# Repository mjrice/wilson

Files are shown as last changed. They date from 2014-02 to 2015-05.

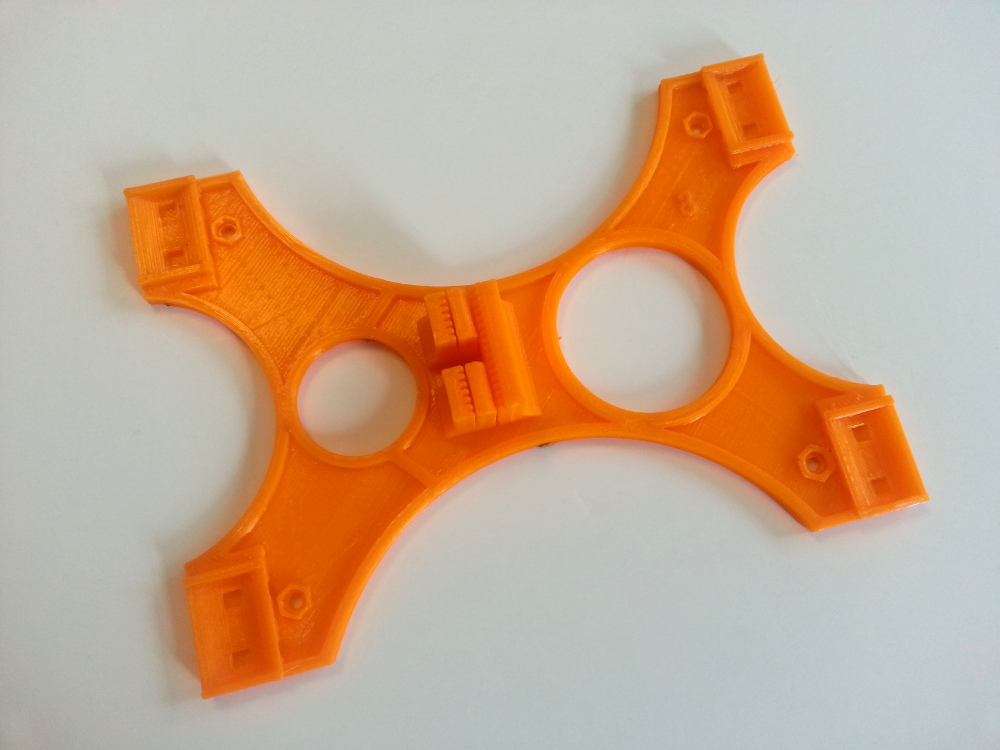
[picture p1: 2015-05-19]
doc/parts-visual/y-table.jpg

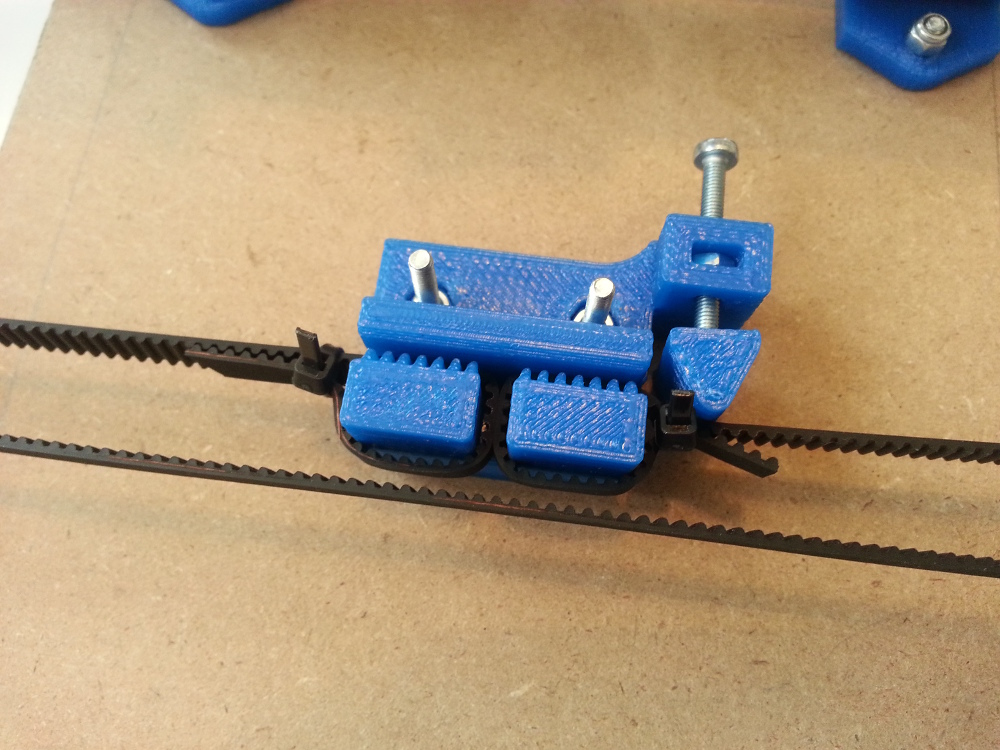
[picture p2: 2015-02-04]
doc/images/ts-belt-holder-assembled.jpg

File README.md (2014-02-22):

wilson
======

Reprap Wilson, 3D printer design
Published under GPL v3

This is my reprap printer design, a derivative from Josef Prusa's i3 with the
following goals:

1.  Replace the waterjet metal frame / wooden box frame with an inexpensive
	and rigid frame made from standard 2020 Aluminum Extrusion.

2.  To make the build volume parametric (easy to scale up or down by 50%), with
	a parametric BOM tool (spreedsheet) to assist in part selection.

3.  To simplify construction of the printer by reducing vitamins and including 
    detailed assembly steps as part of the design files.  I've made an effort 
	to reduce the number of unique parts (nuts & bolts) as much as possible.
	I've also incorporated single-piece Y ends that eliminate about 20 more
	hardware items.

The repository has these parts:

1. The STL files needed to build the printer.
2. Documentation section where instructions and parts-list can be found.
3. Some parts have corresponding OpenSCAD models which are kept in the scad 
   folder.
4. Various images of the printer/build process are in the images folder 
   (beneath docs).

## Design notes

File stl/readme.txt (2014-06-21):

There are two variants of the Repap Wilson design.  Some of the RP parts are common, and those STL files are located in this main directory.

The parts that are specific to one version or the other are located in the respective subfolders.

The BOM will tell you how many of which parts you will need to build the printer.

Notes about updates:

6/21/14 - I've modified a few models described below:

1. The Y belt holder now has a tensioner (yay) affixed to the side. Use
   a M3 x 20 or longer screw and nut to push the little round piece against
   the side of the belt after assembly.  

2. The fan duct for the extruder has been redesigned so that there are 
   separate outlets for the top of the hot end and below the nozzle.  This
   has been working great for me for PLA; ABS prints may not want that lower
   outlet blowing on the print so I'll archive the original fan duct as well.

3. The extruder body itself should now print better.  The opening for the 
   608 bearings on the sides has been marginally increased, as has been the
   J-Head hole on the bottom.  The opening for the hobbed bolt was cleared
   out to remove some extraneous support material.  Also, the distance 
   between the M3 screws for the hot end attachment was decreased by about
   1mm to get a better grip on the J-Head.

4. The Y ends for the TS were changed just a wee bit to make the holes come
   out more suitable (when sliced and printed with a .5mm nozzle) and also
   to add .5mm of height to the feet so that the printer won't tend to rock
   on the central frame.

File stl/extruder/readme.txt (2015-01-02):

Reprap Wilson Extruder files 
----------------------------

The extruder files located here are for the direct-drive extruder that I designed for Wilson.  

The parts for the original geared extruder have been moved to stl/alts.

NOTE!  The default direct-drive extruder is expecting you to use 1.75mm filament.  If you are going to use 3mm filament, I recommend building the geared extruder instead.

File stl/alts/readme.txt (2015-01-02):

wilson/stl/alts - home of old or alternate version of models.  You probably don't need these, unless you do.

belt-guide-sleeve-624.stl                    - An alternate version of the bearing holder.
biggear.stl                                  - Big gear for the Greg's style geared extruder
duct-xlong.stl                               - Another duct option for the extruder
extruder-body-clampmountstyle-1.75mm.stl     - An alternate body for the geared extruder that uses the clamp mount
extruder-body-clampmountstyle.stl            - An alternate body for the geared extruder that uses the clamp mount (3mm filament)
extruder-body.stl                            - The original geared extruder (this is what I used in the original videos)
FAN-DUCT-E3D.stl                             - An attempt to make a fan duct suited to the e3d v6.
FAN-DUCT-widemouth.stl                       - Yet another fan duct
fullgraphicsmartcontroller-mount.stl         - Mounts for the full graphics smart controller 
gregs-wade-v5-mrice-idler-for-M4screws.stl   - The original idler for the geared extruder
idler.stl                                    - The idler for the geared extruder (M3 screws)
smallgear.stl                                - Small gear for the Greg's style geared extruder
nameplate.stl                                - decorative
x-carriage.stl                               - The original X carriage that prints flat (& uses zip ties)
y-bearing-holder-lm10uu.stl                  - An alternate bearing holder if you go with 10mm smooth rods for the y axis
y-bearing-holder.stl                         - The original LM8UU bearing holder that prints flat (& uses zip ties)
y-belt-holder-ts-htd3.stl                    - If you use HTD3 instead of GT2, you need this for the Y belt holder
y-idler-ts-10mm-rods.stl                     - Y idler end for 10mm smooth rods instead of 8mm.
y-motor-ts-10mm-rods.stl                     - Y motor end for 10mm smooth rods instead of 8mm.

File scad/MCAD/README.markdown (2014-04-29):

OpenSCAD MCAD Library (http://stillmaintained.com/elmom/MCAD)
=====================

This library contains components commonly used in designing and moching up
mechanical designs. It is currently unfinished and you can expect some API
changes, however many things are already working.

This library is licensed under the LGPL 2.1
See http://creativecommons.org/licenses/LGPL/2.1/ or the included file, lgpl-2.1.txt.

## Usage ##

You can import these files in your scripts with `use <MCAD/filename.scad>`, 
where 'filename' is one of the files listed below like 'motors' or 
'servos'. Some files include useful constants which will be available 
with `include <MCAD/filename.scad>`, which should be safe to use on all 
included files (ie. no top level code should create geometry). (There is 
a bug/feature that prevents including constants from files that 
"include" other files - see the openscad mailing list archives for more 
details. Since the maintainers aren't very responsive, may have to work 
around this somehow)

If you host your project in git, you can do `git submodule add URL PATH` in your
repo to import this library as a git submodule for easy usage. Then you need to do
a `git submodule update --init` after cloning. When you want to update the submodule,
do `cd PATH; git checkout master; git pull`. See `git help submodule` for more info.

Currently Provided Tools:

* involute_gears.scad (http://www.thingiverse.com/thing:3575):
    - gear()
    - bevel_gear()
    - bevel_gear_pair()

* gears.scad (Old version):
    - gear(number_of_teeth, circular_pitch OR diametrial_pitch, pressure_angle OPTIONAL, clearance OPTIONAL)

* motors.scad:
    - stepper_motor_mount(nema_standard, slide_distance OPTIONAL, mochup OPTIONAL)

Other tools (alpha and beta quality):

* nuts_and_bolts.scad: for creating metric and imperial bolt/nut holes
* bearing.scad: standard/custom bearings
* screw.scad: screws and augers
* materials.scad: color definitions for different materials
* stepper.scad: NEMA standard stepper outlines
* servos.scad: servo outlines
* boxes.scad: box with rounded corners
* triangles.scad: simple triangles

Very generally useful functions and constants:

* math.scad: general math functions
* constants.scad: mathematical constants
* curves.scad: mathematical functions defining curves
* units.scad: easy metric units
* utilities.scad: geometric funtions and misc. useful stuff
* teardrop.scad (http://www.thingiverse.com/thing:3457): parametric teardrop module
* shapes.scad: simple shapes by Catarina Mota

External utils that generate and and process openscad code:

* openscad_testing.py: testing code, see below
* openscad_utils.py: code for scraping function names etc.

## Development ##

You are welcome to fork this project in github and request pulls. I will try to
accomodate the community as much as possible in this. If for some reason you
want collaborator access, just ask.

Github is fun (and easy), but I can include code submissions and other
improvements directly, and have already included code from various sources
(thingiverse is great :)

### Code style ###
I'd prefer to have all included code nicely indented, at least at the block
level, and no extraneous whitespace. I'm used to indent with four spaces as
opposed to tabs or other mixes of whitespace, but at least try to choose a style
and stick to it.

### Testing ###
I've started a minimal testing infrastucture for OpenSCAD code. It's written in
python and uses py.test (might be compatible with Nose also). Just type `py.test`
inside the lib dir in a terminal and you should see a part of the tests passing
and tracebacks for failing tests. It's very simplistic still, but it should test
that no syntax errors occur at least.

The code is included in openscad_testing.py, and can be imported to be
used in other codebases.

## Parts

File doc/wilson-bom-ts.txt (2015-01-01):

Exported bom for Wilson TS from wilson-bom.ods 
Please see the ODS file for details.  
----------------------------------------------

Item                                    Quantity	Length / Notes

2020 Extrusions		
Vertical frame piece (sides)            2           400mm
Horizontal frame piece (top and bottom) 2           330mm
Y axis frame piece (TS only)            2           400mm

M8 Smooth Rods		
X-Axis                                  2           370mm
Y-Axis                                  2           400mm
Z-Axis                                  2           350mm

Threaded Rods		
M5 threaded rod for Z axis              2           325mm

Belts & Pulleys		
Y axis GT2 timing belt (w=6mm)          1           830mm
X axis GT2 timing belt (w=6mm)          1           900mm
GT2 pulley                              2           Want diameter 16-20mm

Nuts & Bolts		
M5 x 10mm machine screw                 51	
M5 hex nut                               2	
M5 t slot nut                           51	
M4 x 20mm machine screw                  7	
M4 hex nut                               7	
M3 x 10mm machine screw                 11	
M3 x 14mm machine screw                 24	
M3 x 30mm machine screw                 10
M3 x 50mm machine screw                  1	   this is for the hinged lever of the direct-dirve extruder
M3 hex nut                              18
M3 lock nut                             13	
M3 washer                               17         This number is approximate
M2 x 16mm machine screw	                 6	   These and M2 nuts for mounting end stops
M2 hex nut	                         6	

Printed Parts – Required		
X end idler                              1	
X end motor                              1	
X carriage                               1	
Y end idler                              1	
Y end motor                              1	
Y belt holder                            1	
Y axis bearing holder                    4         for lm8uu bearings
Z motor holder, left                     1	
Z motor holder, right                    1	
Z rod holder, left                       1	
Z rod holder, right                      1	
Z rear bracket                           2	
Z endstop holder                         1	
Frame brace                              4	
Idler bearing guide (pair)               2	
Extruder body / idler set                1	
Extruder big gear / small gear set       1	
Extruder fan duct                        1	
Belt guides	                         4         (two belt guides, one for each 624 bearing)

Printed Parts – Recommended		
Electronics frame mount (for RAMPS)	1	
Filament spool support (two pieces)	1	
SMART display frame mount (two pieces)	1	

Everything Else		
NEMA17 Stepper motor	                 5	
MDF board (6mm thick)	                 1	230mm by 230mm
Heat bed                                 1 	MK2a or whatever
Heat bed thermistor                      1
Glass bed	                         1	3mm borosilicate or picture frame glass 8.25" square
Controller (Mega/RAMPS, Rambo, etc)	 1	
Endstop (limit) switch	                 3	6mm x 10mm x 20mm
LM8UU Linear bearing	                12	can get away with 11 if you use only three on the X carriage
624 roller bearing                       2	
5mm to 5mm shaft couplers	         2	Can also use vinyl tubing instead
40mm x 40mm x 10mm fan	                 1	12V
80mm x 80mm fan	                         1	For use with RAMPS frame mount
Miniature zip ties	                20	This number is approximate
Extruder idler springs	                 2	High tension 
Bed leveling springs	                 4	Lower tension
Power Supply	                         1	Size appropriately for heat bed and extruder
Hot end	                                 1	Recommend Jhead
MK7 drive gear                           1	omit if you are building the geared extruder (see below)
Printer mount deck (optional)	         1	18” x 18” x 1/2” plywood works well.

The items below are for building with the geared extruder instead of the direct-drive extruder

M3 x 8mm machine screw                   1	for small gear
M3 x 60mm machine screw                  2         
M8 x 20mm smooth rod or grub screw       1	
M8 washers                               5         For alignment of hobbed bolt
M8 locknut                               1         For extruder bolt
Hobbed bolt	                         1	Recommend airwolf3d
608ZZ roller bearing	                 3	

Notes about wires		
The lengths shown are conservative estimates to help you plan for what you'll need		
Extruder heater wire pair	70cm	
Extruder thermistor wire pair	70cm	
Extruder fan wire pair	        70cm	
X end stop wire pair	        25cm	
Y end stop wire pair	        50cm	
Z end stop wire pair	        25cm	
X motor wires (4)	        25cm	motors may be pre-wired in which case you can ignore these probably
Y motor wires (4)	        50cm	''
Z left motor wires (4)	        25cm	''
Z right motor wires (4)	        60cm	''
Extruder motor wires (4)	70cm	
Heat bed power wires	        60cm	12 Gauge or heavier
Heat bed thermistor wires	50cm

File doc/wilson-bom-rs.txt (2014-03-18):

Reprap Wilson RS default parts list
(text export from wilson-bom.ods - use spreedsheet to generate custom bom)
                                                              
Item                              Quantity       Length / Note

2020 Extrusions                                      
Vertical frame piece (sides)             2                 370mm     
Horizontal frame piece (top and bo       2                 330mm     

M8 Smooth Rods                                      
X-Axis                                   2                 380mm     
Y-Axis                                   2                 380mm     
Z-Axis                                   2                 325mm     

Threaded Rods                                       
M5 threaded rod for Z axis               2                 300mm     
M10 threaded rod for Y axis              2                 405mm     

Belts & Pulleys                                      
Y axis GT2 timing belt (w=6mm)           1                 820mm     
X axis GT2 timing belt (w=6mm)           1                 930mm     
GT2 pulley                               2       

Nuts & Bolts                                       
M10 nuts and washers                    12                    
M5 x 10mm machine screw                 36                    
M5 hex nut                               2                    
M5 t slot nut                           36                    
M4 x 20mm machine screw                  6                    
M4 hex nut                               6                    
M3 x 8mm machine screw                   1                    
M3 x 10mm machine screw                 11                    
M3 x 14mm machine screw                 18                    
M3 x 30mm machine screw                  7                    
M3 x 60mm machine screw                  2       50mm ok if your springs are short enough       
M3 hex nut                              20?      
M3 lock nut                              7                    
M8 x 20mm smooth rod or grub screw       1                    

Printed Parts – Required                                 
X end idler                              1                    
X end motor                              1                    
X carriage                               1                    
Y end idler                              1                    
Y end motor                              1                    
Z motor holder, left                     1                    
Z motor holder, right                    1                    
Z rod holder, left                       1                    
Z rod holder, right                      1                    
Z rear bracket                           2                    
Frame brace                              2                    
Idler bearing guide (pair)               2                    
Extruder parts (body, idler, gears, duct) 1 set

Printed Parts – Recommended                                
Electronics frame mount                  1                    
Filament spool support                   1                    
SMART display frame mount                1                    

Everything Else                                      
NEMA17 Stepper motor                     5                    
MDF board (6mm thick)                    1       230mm by 230m
MK2 Heat bed                             1                    
Glass bed                                1       3mm borosilicate
Controller (Mega/RAMPS, Rambo, etc       1                    
Endstop (limit) switch                   3       
LM8UU Linear bearing                    12                    
608ZZ roller bearing                     4                    
624 roller bearing                       2                    
5mm to 5mm shaft couplers                2       Can also use 3/16" ID vinyl tubing
40mm x 40mm x 10mm fan                   1                    
80mm x 80mm fan                          1       
Miniature zip ties                      20       
Extruder idler springs                   2       High tension 
Bed leveling springs                     4       Lower tension
Power Supply                             1

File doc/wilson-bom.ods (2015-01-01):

Reprap Wilson Parametric build parts list
 | Set these values:
Unit system: | metric | ← Enter “metric” or “sae” here
Build variation: | TS | ← Enter “RS” or “TS” here
Desired print width (X): | 200 | mm
Desired print depth (Y): | 200 | mm
Desired print height (Z): | 200 | mm
Direct drive or geared extruder? | direct | ← Enter “direct” or “geared” here
Item | Quantity | Length / Notes
2020 Extrusions
Vertical frame piece (sides) | 2 | 400 | mm | 400
Horizontal frame piece (top and bottom) | 2 | 330 | mm | 330
Y axis frame piece (TS only) | 2 | 400 | mm | 400
M8 Smooth Rods
X-Axis | 2 | 370 | mm | 370
Y-Axis | 2 | 400 | mm | 400
Z-Axis | 2 | 350 | mm | 350
Threaded Rods
M5 threaded rod for Z axis | 2 | 325 | mm
M10 threaded rod for Y axis (RS only) | 0 |  |  | 395
Belts & Pulleys
Y axis GT2 timing belt (w=6mm) | 1 | 830 | mm | 830
X axis GT2 timing belt (w=6mm) | 1 | 900 | mm
GT2 pulley | 2 | Want diameter 16-20mm
Nuts & Bolts
M10 nuts and washers | 0
M5 x 10mm machine screw | 51
M5 hex nut | 2
M5 t slot nut | 51 | the 51-count includes options like filament mount, lcd mount, and ramps mount
M4 x 20mm machine screw | 7
M4 hex nut | 7
M3 x 8mm machine screw | 0 | for extruder small gear (a M3x8mm grub screw may work better)
M3 x 10mm machine screw | 11
M3 x 14mm machine screw | 24 |  |  |  | 19
M3 x 30mm machine screw | 10 |  |  |  | 9
M3 x 50mm machine screw | 1
M3 x 60mm machine screw | 0
M3 hex nut | 18
M3 lock nut | 13
M3 washer | 17 | This number is approximate
M2 x 16mm machine screw | 6 | These and M2 nuts for mounting end stops
M2 hex nut | 6
M8 x 20mm smooth rod or grub screw | 0
M8 washers | 0 | For alignment of hobbed bolt
M8 locknut | 0 | For extruder bolt
Printed Parts – Required
X end idler | 1
X end motor | 1
X carriage | 1
X axis tensioner | 1
Y end idler | 1
Y end motor | 1
Y belt holder | 1
Y axis bearing holder | 4 | for lm8uu bearings
Z motor holder, left | 1
Z motor holder, right | 1
Z rod holder, left | 1
Z rod holder, right | 1
Z rear bracket | 2
Z endstop holder | 1
Frame brace | 4
Idler bearing guide (pair) | 2 | (two belt guides, one for each 624 bearing)
Extruder body / idler set | 1
Extruder big gear / small gear set | 1
Extruder fan duct | 1
Printed Parts – Recommended
Electronics frame mount (for RAMPS) | 1
Filament spool support (two pieces) | 1
SMART display frame mount (two pieces) | 1
ATX power supply mounts | 4 | if mounting standard ATX supply to a deck
Everything Else
NEMA17 Stepper motor | 5
MDF board (heated bed mount) | 1 | 230mm x 230mm x 6mm
MK2 Heat bed | 1 | MK1, MK2, MK2a, MK2b...
Heat bed thermistor | 1
Glass bed | 1 | 3mm borosilicate or picture frame glass
Controller (Mega/RAMPS, Rambo, etc) | 1
Endstop (limit) switch | 3 | 6mm x 10mm x 20mm, “snap action” levered switch
LM8UU Linear bearing | 11
608ZZ roller bearing | 0
624RS roller bearing | 3
MK7 Drive gear (or similar) | 1
5mm to 5mm shaft couplers | 2 | Can also use vinyl tubing instead
40mm x 40mm x 10mm fan | 1 | 12V
80mm x 80mm fan | 1 | For use with RAMPS frame mount
Miniature zip ties | 20 | This number is approximate
Extruder idler springs | 1 | High tension, 1” unsprung length, >3mm ID
Bed leveling springs | 4 | Lower tension is OK, 1” unsprung, ID > 3mm
Z endstop adjustment spring | 1 | Like the bed leveling springs, approx 1”
Power Supply | 1 | Size appropriately for heat bed and extruder
Hobbed bolt | 0 | Recommend airwolf3d
Hot end | 1 | Recommend Jhead
Printer mount deck (optional) | 1 | 18” x 18” x 1/2” plywood works well.
Tools you'll probably need
Phillips screwdriver
Small flat head screwdriver
Metric ruler
13mm wrench
Wire cutters
Small metal (diamond) files | For cleaning up printed parts
Drill
3mm, 5mm, 8mm drill bits | Or 9/64”, 13/64”, and 5/16”
Allen wrenches | If using socket-cap screws for frame, and for pulleys
Pliers
Soldering iron
Kapton tape (polyimide)
Notes about wires
The lengths shown are conservative estimates to help you plan for what you'll need
Extruder heater wire pair | 70cm
Extruder thermistor wire pair | 70cm
Extruder fan wire pair | 70cm
X end stop wire pair | 25cm
Y end stop wire pair | 50cm
Z end stop wire pair | 25cm
X motor wires (4) | 25cm
Y motor wires (4) | 50cm
Z left motor wires (4) | 25cm
Z right motor wires (4) | 60cm
Extruder motor wires (4) | 70cm
Heat bed power wires | 60cm | 12 Gauge or heavier
Heat bed thermistor wires | 50cm

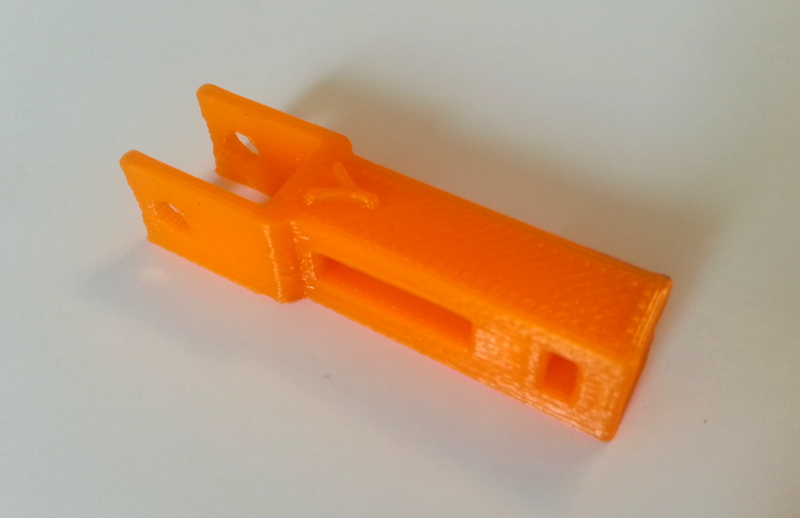
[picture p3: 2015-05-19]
doc/parts-visual/y-belt-tensioner.jpg

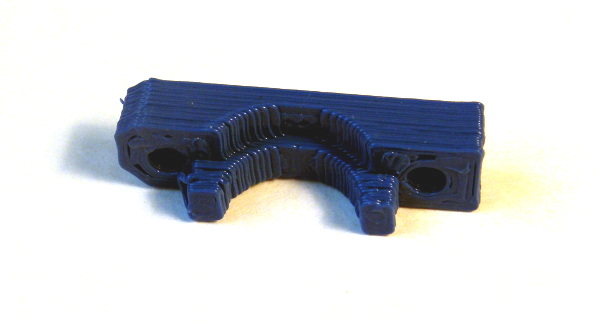
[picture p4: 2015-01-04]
doc/parts-visual/extruder-clamp.jpg

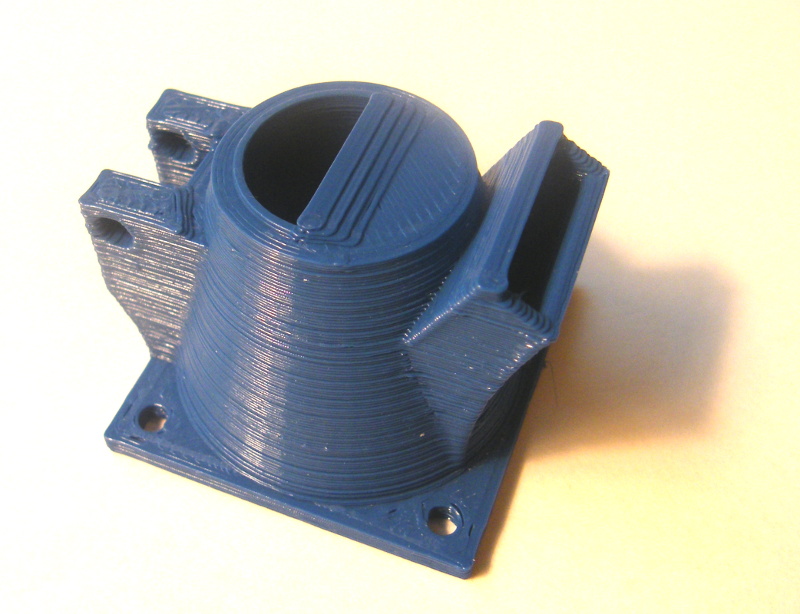
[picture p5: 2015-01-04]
doc/parts-visual/extruder-fanduct.jpg

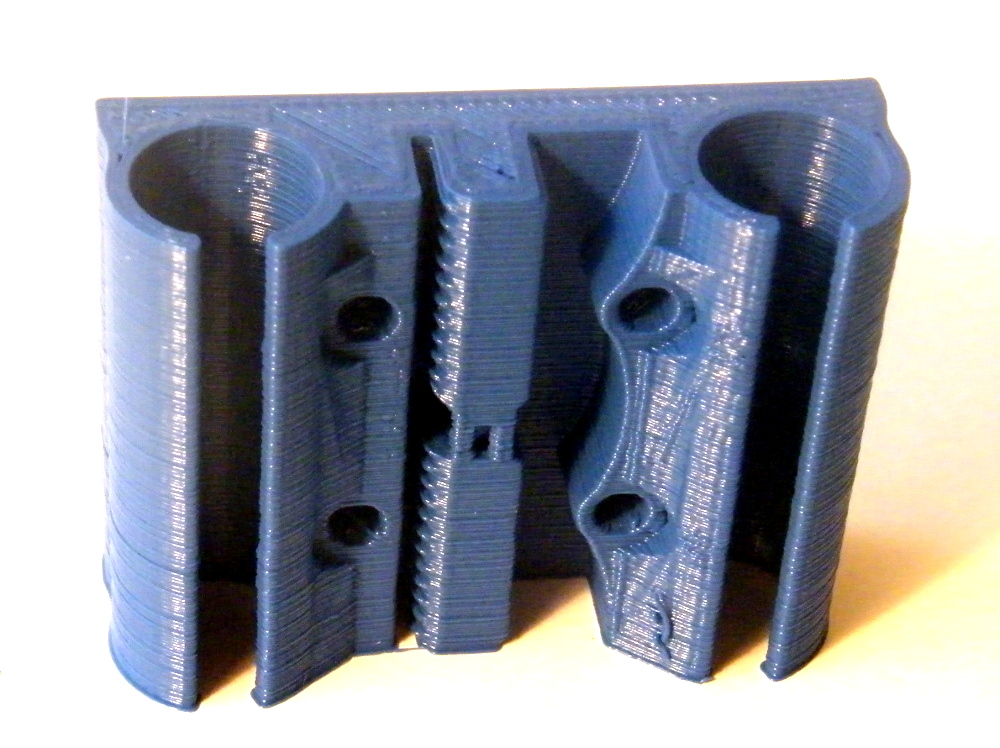
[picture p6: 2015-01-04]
doc/parts-visual/x-carriage.jpg

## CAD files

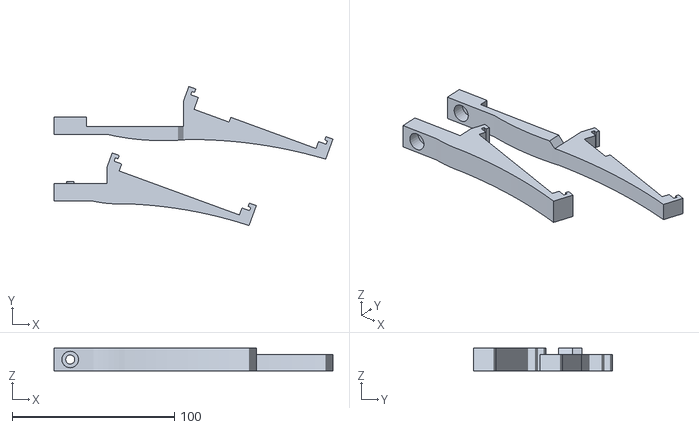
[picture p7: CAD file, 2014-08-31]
stl/alts/fullgraphicsmartcontroller-mount.stl
172.2 x 85.9 x 14.0

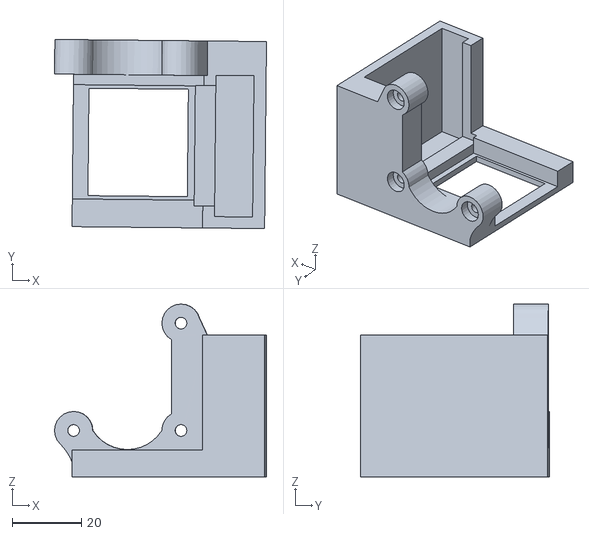
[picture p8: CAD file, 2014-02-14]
scad/i3rsubmotor_fixed.stl
61.2 x 54.6 x 49.9

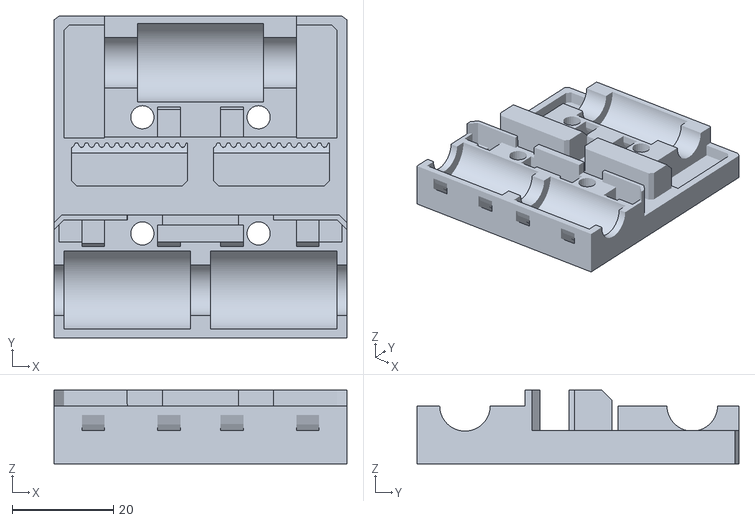
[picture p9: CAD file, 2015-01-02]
stl/alts/x-carriage.stl
58.0 x 63.8 x 14.6

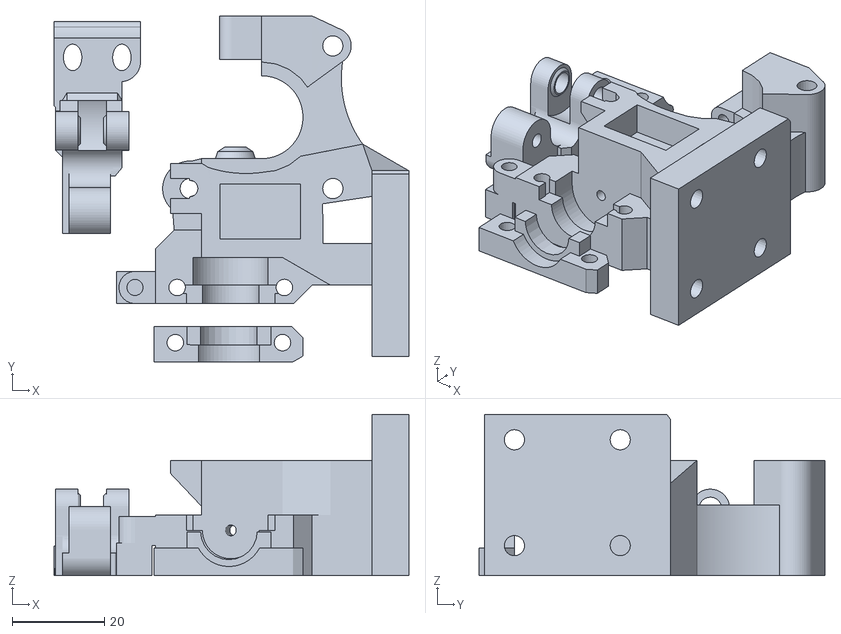
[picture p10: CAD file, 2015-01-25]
stl/extruder/extruder-direct-drive.stl
77.0 x 75.2 x 35.0

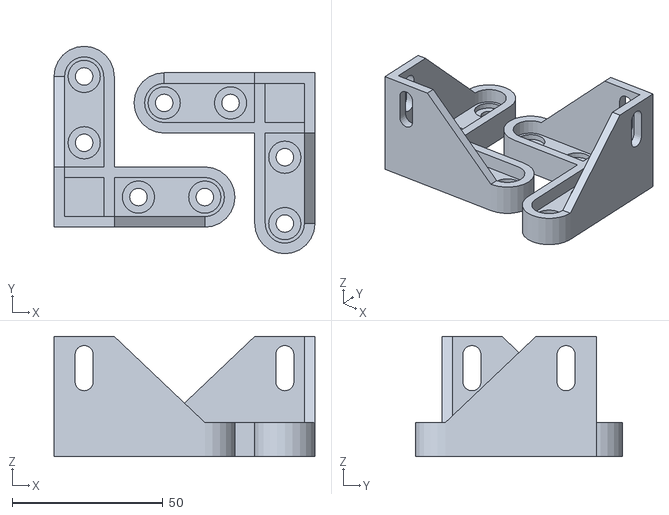
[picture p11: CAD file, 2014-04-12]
stl/rs/frame-rear-bracket-rs.stl
86.5 x 68.8 x 39.8

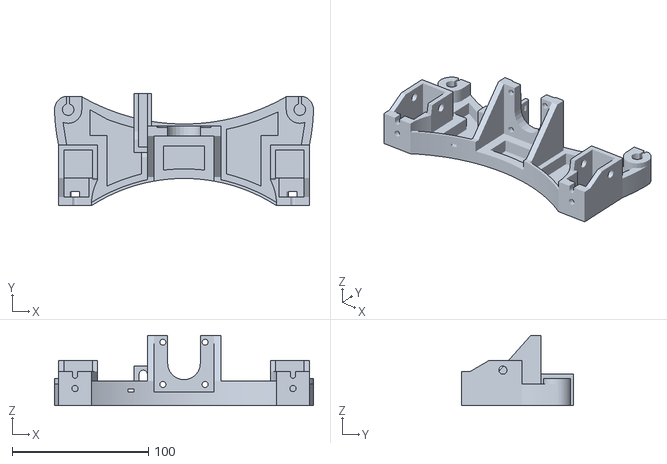
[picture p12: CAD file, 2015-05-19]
stl/ts/y-motor-ts.stl
190.0 x 82.5 x 51.5

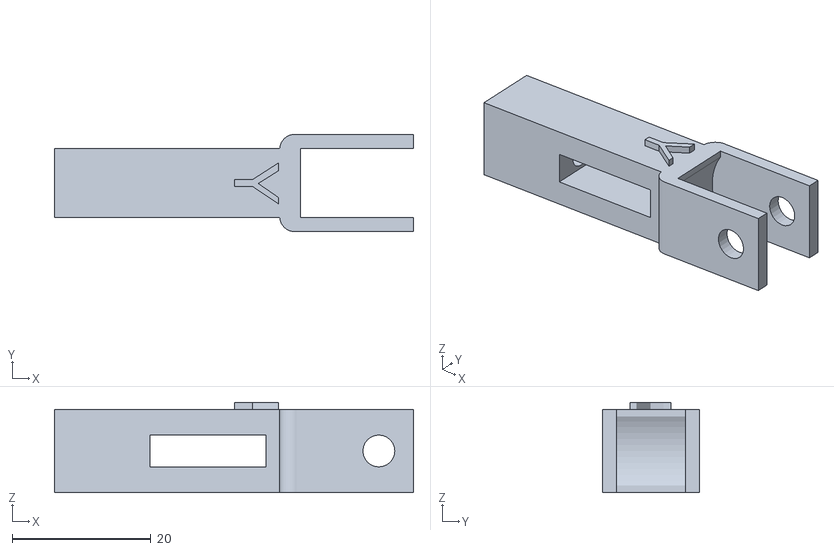
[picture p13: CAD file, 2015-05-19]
stl/y-tensioner.stl
51.8 x 14.0 x 13.0

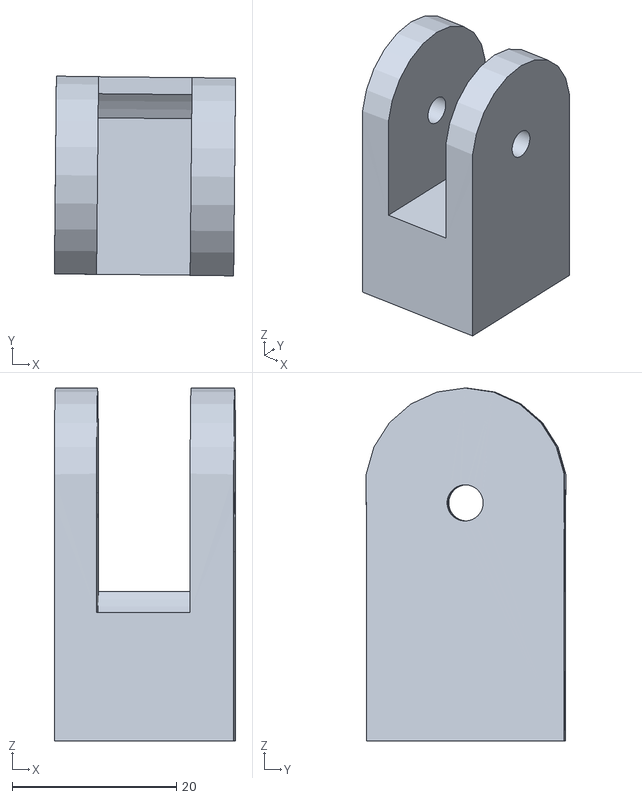
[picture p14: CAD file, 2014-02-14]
scad/i3rsubidler2_fixed.stl
22.1 x 24.3 x 43.0

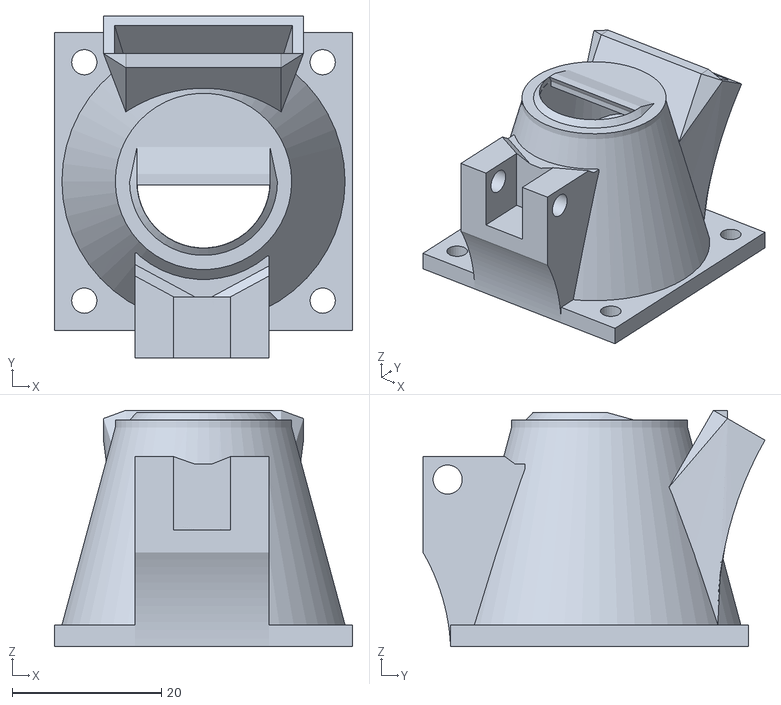
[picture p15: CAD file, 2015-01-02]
stl/alts/FAN-DUCT-widemouth.stl
40.0 x 45.9 x 31.7

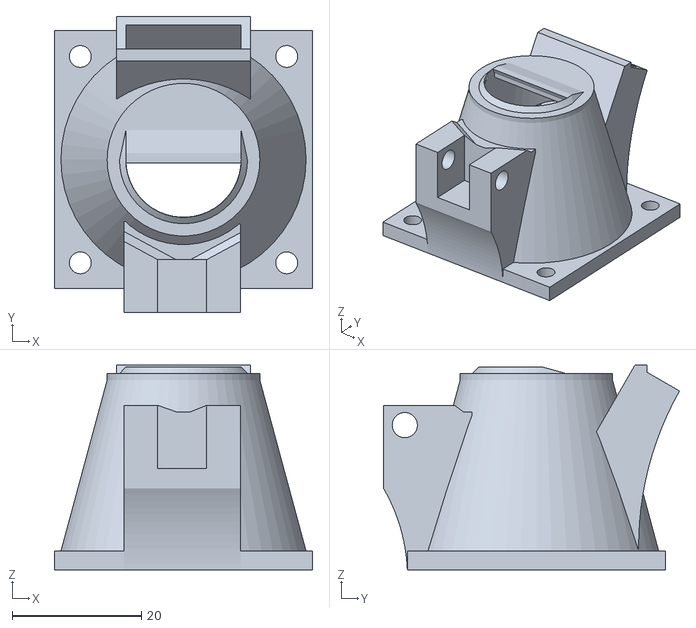
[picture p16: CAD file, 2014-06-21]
stl/extruder/FAN-DUCT.stl
40.0 x 45.9 x 31.7

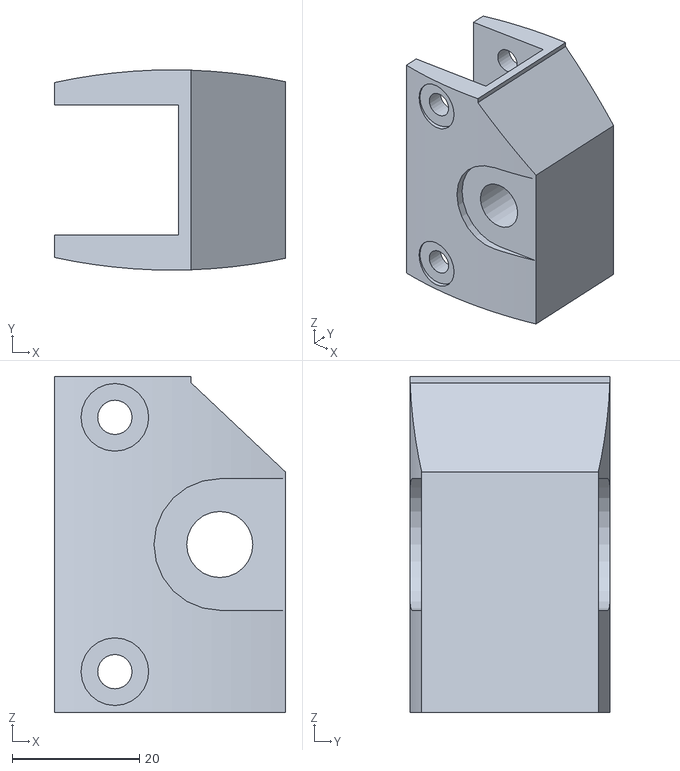
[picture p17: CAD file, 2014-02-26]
stl/rs/frame-beam-bracket.stl
36.3 x 31.5 x 52.8

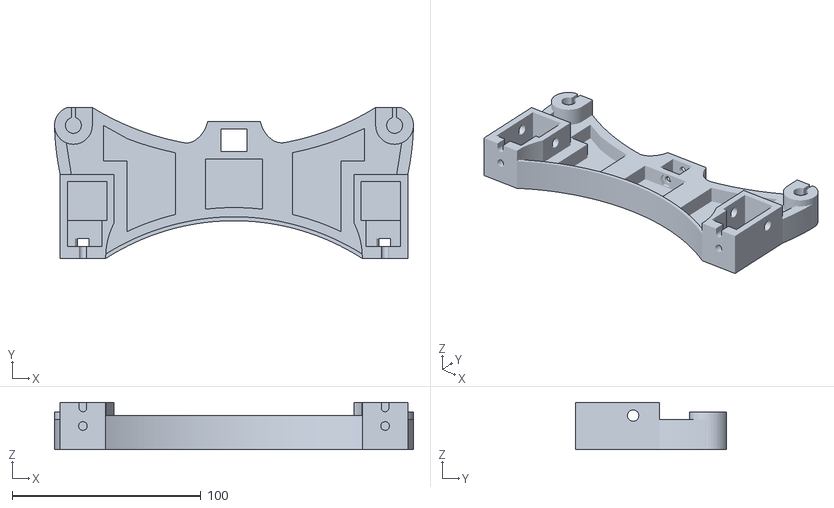
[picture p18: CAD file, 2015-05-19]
stl/ts/y-idler-ts.stl
190.0 x 80.0 x 25.0

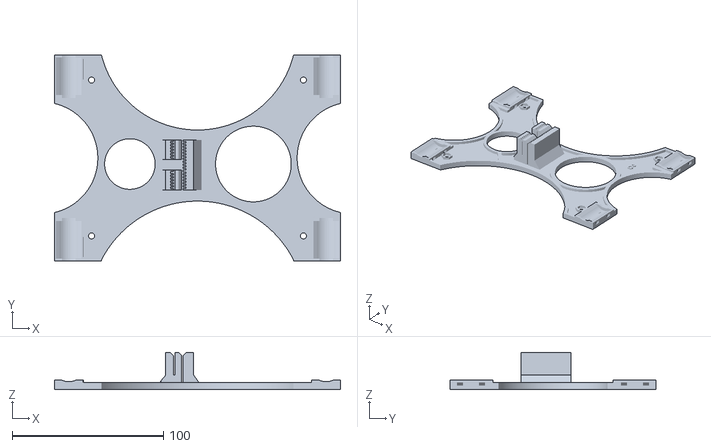
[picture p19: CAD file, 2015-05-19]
stl/ytable-8mm.stl
189.0 x 136.0 x 24.5

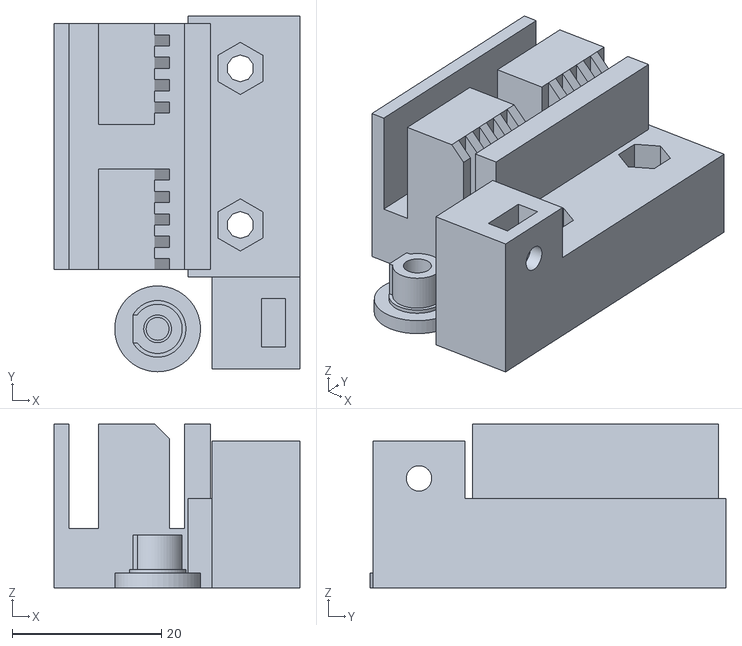
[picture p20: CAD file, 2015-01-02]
stl/alts/y-belt-holder-ts-htd3.stl
33.0 x 47.7 x 22.0

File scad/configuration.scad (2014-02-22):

smooth_rod_d      = 8;
threaded_rod_d    = 10;
tie_wrap_w        = 5;
tie_wrap_t        = 2;
washer_d          = 21;
height_of_threaded = 26.5;
height_of_smooth = height_of_threaded + 11 + 9;
height_of_post = height_of_smooth+2;

belt_width = 6.5;
belt_tooth_distance = 2;
belt_tooth_ratio = 0.5;
belt_thickness = 0.8;

idler_bearing_inner_d = 4; // 624 bearing

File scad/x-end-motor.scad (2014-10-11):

// PRUSA iteration3
// X end motor
// GNU GPL v3
// Josef Průša <iam@josefprusa.cz> and contributors
// http://www.reprap.org/wiki/Prusa_Mendel
// http://prusamendel.org
// Alterations for reprap Wilson by Martin Rice <mrice411@gmail.com>

use <x-end.scad>

offs_adjuster_y = 5.5;
adj_block_x = 12;
adj_block_y = 10;
adj_block_z = 32;
motor_offs_z = 0;

module adjustomatic() {

   difference() {     
       translate(v=[-(15+17/2+adj_block_x/2),offs_adjuster_y,58-adj_block_z/2]) 
          cube(size=[adj_block_x,adj_block_y,adj_block_z],center=true);
       
       translate(v=[-(15+17/2+adj_block_x/2)-5,offs_adjuster_y,58-adj_block_z/2-8]) 
         rotate([0,-30,0]) cube(size=[adj_block_x,adj_block_y+2,adj_block_z],center=true);

       translate(v=[-(15+17/2+adj_block_x/2-1),offs_adjuster_y,58-adj_block_z/2-3]) 
          cube(size=[adj_block_x,adj_block_y-2,adj_block_z-2],center=true);

       translate(v=[-(15+17/2+adj_block_x/2),offs_adjuster_y,58-adj_block_z/2+14]) 
           {
         rotate([0,0,30]) #cylinder(h = 4, r = 7.5/2 , $fn = 6);
         translate([0,0,-20]) #cylinder(h=30,r=2,$fn=16);
}

   }

}

module pocket_endstop()
{
translate([-7,-40,0]) 
    difference() {
       union() {  translate([-1.5,0,0]) cube(size=[9,16,22]);
                  //translate([3,12,20]) cylinder(r=4,h=10,$fn=16);
                  translate([-11,40,57.9]) rotate([90,0,0]) cube(size=[10,5,20]);
       }
    
    #translate([-2,-1,1]) cube(size=[7,16,22]);
    //#translate([3,12,20]) cylinder(r=3,h=21,$fn=16);
    // grove for wiring along bottom
    #translate([-10,50.5,58]) rotate([90,0,0]) cube(size=[8,4,31]);
    // screw holes for endstop switch
    #translate([-2,7,1.5+5.5]) rotate([0,90,0]) cylinder(r=1.5,h=15);
    #translate([-2,7,1.5+5.5+9.5]) rotate([0,90,0]) cylinder(r=1.5,h=15);
    //#translate([0,-3,15]) cube(size=[6,15,20]);
    }
}

module x_end_motor_base(){
 x_end_base();
 // motor arm
 translate(v=[-15,31,26.5+motor_offs_z]) cube(size = [17,44,53], center = true);
 // z stop adjuster
 adjustomatic();
 // x endstop holder
 pocket_endstop();
}

screw_head_r = 3.5;

module x_end_motor_holes(){
 x_end_holes();
 // Position to place
 translate(v=[-1,32,30.25+motor_offs_z]){
  // Belt hole
  translate(v=[-14,1,0]) cube(size = [10,46,22], center = true);
  // Motor mounting holes
  translate(v=[20,-15.5,-15.5]) rotate(a=[0,-90,0]) rotate(a=[0,0,90]) cylinder(h = 70, r=1.8, $fn=30);
  translate(v=[1,-15.5,-15.5]) rotate(a=[0,-90,0]) rotate(a=[0,0,90]) cylinder(h = 12, r=screw_head_r, $fn=30);
 

  translate(v=[20,-15.5,15.5]) rotate(a=[0,-90,0]) rotate(a=[0,0,90]) cylinder(h = 70, r=1.8, $fn=30);
  translate(v=[1,-15.5,15.5]) rotate(a=[0,-90,0]) rotate(a=[0,0,90]) cylinder(h = 12, r=screw_head_r, $fn=30);


  translate(v=[20,15.5,-15.5]) rotate(a=[0,-90,0]) rotate(a=[0,0,90]) cylinder(h = 70, r=1.8, $fn=30);
  translate(v=[1,15.5,-15.5]) rotate(a=[0,-90,0]) rotate(a=[0,0,90]) cylinder(h = 12, r=screw_head_r, $fn=30);


  translate(v=[20,15.5,15.5]) rotate(a=[0,-90,0]) rotate(a=[0,0,90]) cylinder(h = 70, r=1.8, $fn=30);
  translate(v=[1,15.5,15.5]) rotate(a=[0,-90,0]) rotate(a=[0,0,90]) cylinder(h = 12, r=screw_head_r, $fn=30);

  // Material saving cutout 
  translate(v=[-10,12,10]) cube(size = [60,42,42], center = true);

  // Material saving cutout
  translate(v=[-10,40,-30]) rotate(a=[45,0,0])  cube(size = [60,42,42], center = true);
  // Motor shaft cutout
  translate(v=[0,0,0]) rotate(a=[0,-90,0]) rotate(a=[0,0,90]) cylinder(h = 70, r=17, $fn=6);

  // zip tie retainer for securing end stop wiring
  #translate([-5,-59,14]) difference() { cylinder(r=4.5,h=4,$fn=16);
                                          translate([0,0,-1]) cylinder(r=2.5,h=7,$fn=16);
                                        }
 }
}

// Final part
module x_end_motor(){
 difference(){
  x_end_motor_base();
  x_end_motor_holes();
 }
}
rotate([0,0,180])
x_end_motor();

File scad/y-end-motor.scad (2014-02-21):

//
// Parametric single-piece y ends for Reprap Wilson
// GNU GPL v3
// by Martin Rice <mrice411@gmail.com>
//
include <configuration.scad>

washer_recess     = 2; // recesses the washer into the outer side of the end.
motor_face_x_offs = 78; // distance from corner to the face of the stepper motor
fan_hole          = 1;
strengthen_around_fan = 1; // adds block behind fan for extra stiffness
brace_h            = 41;
want_endstop_mount = 1;    // set to zero if you don't want it!
fan_depth = 10; // if this is greater than 10mm, be sure to add strengthen from above.
end_w = 193.5;
tie_wrap_extra = 1;

//endpost();
yend_motor();

module yend_motor()
{
  difference() {
    union() {
       // thin base under the end (optional)
       bigbase();
       // first corner
       endpost();
       // second corner
       translate([end_w,0,0]) scale([-1,1,1]) endpost();
       // motor and fan mount
       translate([motor_face_x_offs,0,0]) translate([-60,42.52,-3]) rotate([0,0,-89.4]) import("i3rsubmotor_fixed.stl");
   
       // connecting braces
       translate([88+53,-3,0]) cube([29.5,19,brace_h]);
       translate([88,0,0]) brace();
       translate([23,0,0]) smallbrace();

       if(strengthen_around_fan)    {        
          translate([25+9.2,-5-(fan_depth-10),0]) cube([54,6+(fan_depth-10),brace_h]);
       }

       if(want_endstop_mount) {
           translate([157,3,brace_h-1]) {
                  cube([4,13,20]);
                  translate([0,10,0]) rotate([0,0,90]) cube([3,5,20]);
           }
          
       }

     }

     // bevels on outer corners
     translate([-1,-23/2,-1])    rotate([0,0,45]) cube([10,10,90]);
     translate([end_w+1,-23/2,-1]) rotate([0,0,45]) cube([10,10,90]);
     translate([43,21,-1]) cube([32,30,10]);
     
     // fancy big cutout
     translate([88+23+(fan_depth-10)/5,-45.4-(fan_depth-10)/3,-1]) cylinder(r=52,h=brace_h+10,$fn=100);

     // fan cutout for bigger fans
     #translate([25+13,4+10-fan_depth,1]) cube([40,fan_depth+.5,40]);
     
     // fan vent cutout
     if(fan_hole) translate([23+23.7+11.2,5,20]) rotate([90,0,0]) cylinder(r=19,h=40,$fn=6);

     if(want_endstop_mount) {
            #translate([160,3,brace_h]) {
                translate([1.1,0,1]) cube([6,15,20]); // endstop for visualization
                translate([-5,6.5,5]) #rotate([0,90,0]) rotate([0,0,30]) cylinder(r=1.8,h=10); // mount hole
                translate([-5,6.5,15]) #rotate([0,90,0])  rotate([0,0,30]) cylinder(r=1.8,h=10); // mount hole
             }
            
     }
  }
}


module endpost()
{
     difference() {
       union() {
         difference() {
           cube([23,16,height_of_post]);
           #translate([23/2,7,height_of_post]) rotate([-90,0,0]) cylinder(r=smooth_rod_d/2+2+tie_wrap_t+tie_wrap_extra,h=tie_wrap_w);
         }

         difference() {
         translate([23/2,7,height_of_post]) rotate([-90,0,0]) cylinder(r=smooth_rod_d/2+2+tie_wrap_extra,h=tie_wrap_w);
         translate([0,0,height_of_post]) cube([23,16,10]);
         }
       }

       translate([23/2,-10,height_of_threaded ]) rotate([-90,0,0]) cylinder(r=threaded_rod_d/2+.4,h=380);
       translate([23/2,-.1,height_of_threaded ]) rotate([-90,0,0]) cylinder(r=washer_d/2+.4,h=washer_recess);
       translate([23/2,2.5,height_of_smooth]) rotate([-90,0,0]) cylinder(r=smooth_rod_d/2+.1,h=380);
     }

}

module bigbase()
{     
       intersection() {
       cube([193.5,55,2]);
       translate([end_w/2,-85,-1]) cylinder(r=140,h=9,$fn=50);
       }
}

module brace()
{   

   difference() {
      translate([0,-3,0]) cube([53,19,brace_h]);
      //translate([25,-45.4,-1]) cylinder(r=52,h=brace_h+2,$fn=100);
      translate([25,61.5,-1]) cylinder(r=52,h=brace_h+2,$fn=100);
   }
 
}

module smallbrace()
{
      smallbrace_h = brace_h;

     cube([11.2,16,smallbrace_h]);
}

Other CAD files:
stl/extruder/FAN-DUCT-ORIG.stl
stl/rs/y-end-idler.stl
stl/ts/frame-rear-brackets-ts-pair.stl
stl/x-carriage-pushfit.stl
scad/bearing.scad
scad/MCAD/2Dshapes.scad
scad/MCAD/bearing.scad
scad/MCAD/bitmap/alphabet_block.scad
scad/MCAD/bitmap/bitmap.scad
scad/MCAD/bitmap/height_map.scad
scad/MCAD/bitmap/letter_necklace.scad
scad/MCAD/bitmap/name_tag.scad
scad/MCAD/boxes.scad
scad/MCAD/constants.scad
scad/MCAD/curves.scad
scad/MCAD/gears.scad
scad/MCAD/gridbeam.scad
scad/MCAD/hardware.scad
scad/MCAD/involute_gears.scad
scad/MCAD/layouts.scad
scad/MCAD/libtriangles.scad
scad/MCAD/materials.scad
scad/MCAD/math.scad
scad/MCAD/metric_fastners.scad
scad/MCAD/motors.scad
scad/MCAD/nuts_and_bolts.scad
scad/MCAD/regular_shapes.scad
scad/MCAD/screw.scad
scad/MCAD/servos.scad
scad/MCAD/shapes.scad
scad/MCAD/stepper.scad
scad/MCAD/teardrop.scad
scad/MCAD/triangles.scad
scad/MCAD/units.scad
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

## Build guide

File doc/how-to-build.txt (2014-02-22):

Reprap Wilson Assembly Guide
Written by Martin Rice <mrice411@gmail.com>

+ For the latest version of this document, check the "docs" folder at     +
+ https://github.com/mjrice/wilson                                        +
+                                                                         +
+ Please refer to the wilson-bom spreedsheet for a comprehensive list of  +
+ parts needed before you begin.                                          +
+                                                                         +
+ You will find photos of most of the steps below indexed by the step     +
+ number, located in the images/ folder.                                  +

1. Assemble the Y axis (part 1)

1.1 Gather the following parts

	a. The two M10 threaded rods
	b. The Y axis smooth rods
	c. The plastic Y end pieces (2)
	d. The two plastic frame brace supports
	e. 12 M10 nuts and washers
	f. Four linear bearings (LM8UU) 

1.2 Hardware Assembly

*	Slide a brace support onto each threaded rod. On each side of the 
	supports, put a washer, a nut, another nut and another washer (in 
	that order).
*	Next, slide two two Y end pieces over the ends of the threaded rods. 
	Place a washer then nut on each end.

1.3 Tightening the Y axis

*	Start at one end (either Y motor or Y idler end) and tighten the two 
	nuts against the end so that the threaded rod is flush with the outside 
	of the nut. Tighten both sides of the first end while everything else 
	is loose along the threaded rods. Use two wrenches  to tighten the nuts 
	against the end until snug (tight, but don't compress enough to deform 
	or break the plastic).
*	Place two linear bearings on each Y axis smooth rod.
*	Next, with the other Y end still loosely attached, place the two Y axis 
	smooth rods across the top and fit into the grooves along the top of 
	the ends.
*	Press down on the corners (not in the middle of the rods!) to seat the 
	rods into the Y ends.
*	Tighten one corner of the remaining end.
*	Now take a moment to measure with a ruler between the end posts of the 
	tightened side. (355mm for reference).
*	Flip the assembly around and repeat the measurement as you tighten the 
	remaining corner (tighten it just a little first, then measure. If the 
	distance is a little less than the first side, tighten the inner nut 
	outward toward the outer nut, if the distance is a little more than the 
	first side, then tighten the outer nut toward the inner one. Try to get 
	the two sides as close to the same distance as possible. This will help 
	ensure your y axis bearings don't experience any binding forces).
*	Repeat the measurement on the first side and check that all corners are 
	nice and snug. Take your time on this step, it may require a couple 
	iterations to get the axis square. 

1.4 Prep the Print Bed

While the Y axis assembly is free, it is a good time to prepare the print 
bed which you will attach later.

Gather the following materials

	a.	The Y axis assembly you just completed
	b.	The wood print bed support
	c.	The heat bed
	d.	The four linear bearing holders
	e.	Eight miniature zip ties 

*	Place the heat bed circuitboard over the wood bed and mark the four 
	corner locations with a pencil.
*	Put the heat bed circuitboard aside and place the four linear bearing 
	holders over the linear bearings along the Y axis rods.
*	Turn the Y axis assembly over so that the smooth rods (and bearing 
	holders) are against the wood print bed surface.
*	Align the front edge of the two bearing holders nearest the Y end idler 
	with a line that is 80mm from the front edge of the bed.
*	Align the back edge of the two bearing holders nearest the Y end motor 
	mount with a line that is approx 10mm from the back edge of the bed.
*	Mark all the holes for the bearing holders with a pencil.
*	Remove the wood print bed and drill all the holes you marked with a 5mm 
	drill bit. (You want the holes a little over-sized so that there is 
	some room for the screws to "float" when you attach the bed).
*	Attach the linear bearing holders to the Y axis linear bearings with 
	zip ties.

Set the prepared wood print bed aside.

2. Assemble the Frame (part 1)

2.1 Gather the following parts

	a.	The two side pieces of 2020 aluminum extrusion (the longer ones, 
		generally)
	b.	One of the two horizontal pieces of 2020 aluminum extrusion (the 
		shorter ones, generally)
	c.	22 T-slot nuts
	d.	14 M5 x 8mm screws
	e.	The plastic Z motor holders (2)
	f.	The plastic rear frame brackets (2) 

2.2 Hardware Assembly 

*	Slide 6 T-nuts into one side of the shorter extrusion (this wlll be the 
	bottom piece of the frame).
*	Turn the extrusion over (being careful not to let the nuts slide out 
	that you just put in) and slide 8 more nuts into the opposite side that 
	you begain with.
*	Place the two remaining extrusions to the sides of the first, and slide 
	two T nuts into each on the side facing up.
*	Get the two corner braces and place one over each corner. Line up the 
	two nuts on each extrusion and attach the braces with a total of 8 M5 
	screws. Note that the longer extrusions (the "sides" of the frame) 
	should cover the ends of the bottom extrusion piece. Leave the screws 
	loose until all 8 are started. 
*	Stand the frame "upright" to ensure the sides are slid down flush with 
	the bottom and alternately tighten until all the screws are tight.
*	Rotate the frame so the other side is facing you and put it back flat 
	on your work surface.
*	Slide two more T nuts into each side piece and attach the motor mounts 
	the same way you did the rear brackets, using 6 more M5 screws.
*	You should have four T nuts sliding around between the lower corners, 
	which will be used to attach the Y axis to the frame in the next step.

3. Mount the Y axis to the frame

3.1 The following parts are used during this step: 

	a.	The partially-assembled Y axis from step 1. 
	b.	The partially assembled frame from step 2. 
	c.	Eight M5 x 8mm screws 	

3.2 Mounting the Y axis

*	Place the Y axis over the frame so that the Y motor end is toward the 
	rear, and the Z motor brackets are toward the front. 	
*	Slide the Y axis along the threaded rods so that there is ** 135mm **
	from the Y motor end and the frame braces 	
*	Tighten the nuts on the first side finger-tight against the frame brace 
	then turn the assembly around and repeat on the other side. Measure a 
	couple times to make sure the distance from the y motor end to the frame 
	braces is the same on each corner. Next slide the Y axis assembly left 
	or right along the lower frame extrusion so that there is ** 50mm ** 
	from the upright extrusion to the inner edge of the frame brace on the 
	"left" side of the printer (as viewed with the Y axis idler toward you). 	
*	Tighten the frame braces using 8 M5 screws into the T slot nuts that 
	are alread in the lower frame extrusion. Finish tightening the nuts of 
	the threaded rod against the braces, double-checking that the distance 
	from the Y end to the braces is the same on each side. A convenient 
	place to measure this after the nuts are snug is from the inside of the 
	nuts (approx 116mm). 	

4. Assemble the X axis (part 1)

4.1 Gather the following parts: 

	a.	The two plastic X end pieces ("motor" and "idler") 
	b.	Eight linear bearings (LM8UU) 
	c.	The two X axis smooth rods 
	d.	Two M5 nuts
	e.	X endstop limit switch
	f.	One M3 x 30mm screw and nut
	g.	One spring 	

4.2 Hardware Assembly

*	Press two linear bearings into each X end. 
*	Using pliers, gently press an M5 nut into the provided insert in each 
	end. 
*	Place two linear bearings on each of the smooth rods. 
*   Insert the X endstop switch (previously wired) into the slot provided
	on the X motor end.  Route the wires down and through the guide on
	the bottom side of the end.  Secure with a zip tie.
*	Press an M3 nut into the bottom of the Z axis adjuster, then thread 
	an M3 x 30mm screw through a spring and into the nut from the top side.
*	Press each X end onto the pair of smooth rods, being sure to orient 
	them so that the M5 nuts are on the same side of the rods. 	

5. Assembling the frame (part 2)

5.1 Gather the following: 

	a.	The two upper Z axis mounts. 
	b.	The remaining piece of aluminum extrusion (the top bar) 
	c.	Four t-slot nuts 
	d.	Five more t-slot nuts if you are going to use the filament holder 
		and SMART electronics mount. 
	e.	Four M5 x 8mm screws 	

5.2 Assembly

*	Insert two t-slot nuts into the top side of the aluminum extrusion. 
*	If you will be using the filament holder, rotate the extrusion 90 
	degrees and insert two more t-slot nuts into the top side. 
*	Insert the remaining t-slot nuts into the side opposite from the one 
	you started with. 
*	Attach the upper Z axis mounts to the ends of the extrusion, tightening 
	the M5 nuts just until snug. Be sure to keep the two t slot nuts for 
	the filament holder on the "top" and the t slot nuts for the SMART 
	electronics mount and filament holder to the back (side away from the 
	rod holders).

6. Mounting the X axis to the Z axis

6.1 Gather the following

	a.	The partialy assembled frame from step 3.
	b.	The X axis assembly from step 4.
	c.	The upper frame assembly from step 5.
	d.	The remaining two smooth rods
	e.	The Z axis threaded rods (M5)
	f.	Two NEMA17 stepper motors
	g.	Eight M3 x 10mm screws (washers recommended)
	h.	Two Z axis couplers (either 5mm x 5mm couplers or 3/16" vinyl tubing)
	i.	Eight t-slot nuts
	j.	Eight M5 x 8mm screws 

6.2 Mounting the X axis onto the frame.

*	Attach the two Z axis motors to the motor mounts using four M3 x 10mm 
	screws each. Place the z axis couplers on each motor shaft.
*	Press each Z axis smooth rod firmly down into the rod holder of each motor 
	mount, being careful to keep the rods straight up and down to avoid 
	breaking the mounts.
*	Gently slide the X axis assembly down over the Z axis rods. If the linear 
	bearings in each X end do not align with the Z axis rods, remove the X 
	axis assembly and gently push/pull the two ends to get the distance right. 
	The motor end of the X axis assembly should be on your left (with the Y 
	idler end toward you).
*	Insert two t-slot nuts into both the front and back sides of each end (8 
	total). You may want to hold the frame assembly on your lap with the 
	upright extensions horizontally at the point, so that the t slot nuts 
	don't slide down to the botttom of the frame. If they do, simply place 
	your hands over the tops of the extrusions, keeping the z axis smooth 
	rods supported, and tip the assembly over to slide the nuts back toward 
	the top.
*	Place the upper frame assembly on the frame. Fit the tops of the z axis 
	smooth rods into the rod holders.
*	Secure the top of the frame using 8 M5 x 8mm screws. Be sure to press 
	the top of the frame down securely onto the vertical extrusions, and 
	then press inward on each top corner to seat the upper extrusion against 
	the sides.
*	With the X axis assembly resting at the bottom of the Z axis smooth 
	rods, thread the z axis threaded rods down through the nut in each X 
	end until the threaded rods rest against the Z axis motor shafts. 
*	Tighten the z axis couplers. 

7. Completing the Frame Assembly

7.1 Mount X and Y motors

*	In addition to the frame from the previous step, gather the following:

	a.	Two NEMA17 stepper motors
	b.	Two belt pulleys
	c.	The two idler bearings and plastic bearing guides
	d.	Three M3 x 10mm screws
	e.	Three M3 x 14mm screws
	f.	Two M4 x 20mm screws and nuts

*	Mount the motors to the X and Y axis motor mounts using three screws 
	each.  
*	Fit a pulley on each motor shaft and tighten the grub screws to keep 
	them secure.
*	Snap an idler bearing into each pair of plastic bearing guides, then
	attach the idlers to the opposite ends of the X and Y axis from where
	you attached the motors.  Don't overtighten the screws that hold on
	the idlers.

7.2 Attach print bed

*	You will need:

	a.	The print bed you prepared earlier.
	b.	Eight M3 x 14mm screws and an equal number of M3 nuts and washers.

*	Mount the print bed to the Y axis bearing holders.	The washer should 
	go on the screw first, which should go downward through the wood print 
	bed and bearing holder, and secured with a nut.  Attach each screw only 
	loosely first, then check that the bed slides smoothly back and forth 
	along the Y axis. Tighten the nuts a little at a time until secure. 	

7.3 Attach the X carriage.

*	You will need:

	a.	The printed X carriage
	b.	Eight miniature zip ties 

* 	Attach the X carriage with the belt guide "up" and with the flat 
	surface (where you will attach the extruder) toward the front of the
	printer (the Y idler end).
	
7.4	Attach Belts

*	You will need:

	a.	The X axis drive belt
	b.	The Y axis drive belt
	c.	The Y belt holder
	d.	8 Miniature zip ties

*	Thread the X axis belt into place and secure with four zip ties (two
	on each side of the extruder, trimmed short after tight).
*	Turn the printer over or have a friend hold it upside down, being 
	careful not to lift by or put pressure on the X axis rods.  
*	Thread the Y axis belt into place.  Hold the belt tight and use as a
	guide for placing the Y belt holder.  The leading edge of the belt 
	holder should be approximately in the middle of the wood print bed.
*	Mark the holes for the Y belt holder, then set the holder and belt 
	aside and drill the two holes with a 4-5mm hand drill.  
*	Attach the Y belt holder with the head of the screws to the bottom,
	with a washer and nut on the wood side.  

7.5	Attach accessory mounts

*	You will need:
	a.	Filament holder mounts
	b.	SMART display mounts
	c.	RAMPS electronics frame mount
	c.	Eight M5 x 8mm screws

7.6	Attach heat bed

*	You will need:

	a.	The heat bed circuitboard
	b.	Four M3 x 30mm screws and locknuts
	c.	Four springs (approx 1" long uncompressed)

* 	This is a good time to attach the heat bed thermistor if you have not
	already done so.  Depending on your heat bed and thermistor, the most
	likely procedure here is to secure the thermistor to the middle of the
	bottom-side of the heat bed with a strip of Kapton tape.  
*	Attach the heat bed with a screw through each corner, with the head of
	the screw up, down through the heat bed, through a spring, then through 
	the wood print bed, and into a lock nut.  Compress the springs about 
	halfway (you will adjust each corner later to level the bed more 
	precisely).

7.7	Attach Limit Switches

*	You will need:

	a.	Three micro limit switches
	b.	The Z axis limit switch mount
	c.	One T-slot nut and M5 x 8mm screw
	c.	M2 x 16mm screws and nuts as needed (up to 6 each)

*	If your limit switches do not already have wires attached, do that
	now.  You will need approximately 45cm (18") of wire on each switch
	(depending on where you locate the electronics).

*	Slide a T nut into the outer side of the left upright piece from
	the bottom.  Attach the Z endstop holder with a M5 x 8 screw.

8.	Extruder Assembly and Mounting

8.1 Assemble the Extruder

*	You will need:

	a.	The extruder body and idler.
	b.	The hot end.
	c.	The M8 Hobbed bolt
	d.	Two M8 nuts (or one M8 locknut), and washers (probably 4).
	e.	Two springs (approx 1" long uncompressed)
	f.	The M8 x 20mm smooth rod (or M8 x 20mm grub screw)
	g.	Three 608 bearings
	h.	Two M3 x 60mm screws 
	i.	The larger extruder gear.
	j.	Three M3 x 30mm screws
	k.	Five M3 nuts

*	If your hot end was not previously assembled (heater resistor and 
	thermistor), do that now.  Follow the instructions for your particular
	hot end.
*	Slide the M8 x 20mm shaft through a 608 ball bearing then push this 
	assembly inside the extruder idler. You may have to use pliers to snap
	the shaft into place.  Apply even pressure on top of the shaft/bearing
	to avoid cracking the plastic idler.
*	Insert an M3 nut into the inner recess provided on the idler.  Use 
	pliers or a hot iron to fix the nut into place (be careful not to break
	the idler in the process).  
*	Thread an M3 x 30mm screw through the outer side of the idler on the
	side you just inserted the nut, just until the screw starts into the 
	nut.
*	Fix the idler assembly to the Wade Body Extruder and then finish 
	screwing the M3 x 30 bolt all the way through the fulcrum support.

*	Slide the Wade Big Gear through the hobbed bolt so that the hex head of
	the bolt is secured in the recess of the big gear.  Slide 3-5 M8 washers
	onto the bolt (they go between the gear and the body of the extruder to
	provide spacing) followed by one 608 bearing.  Insert the bolt into the
	extruder body, securing the bearing in the hole provided.  Add another 
	608 bearing on the loose end of the bolt, followed by another M8 washer 
	and	locknut.  Tighten the lock nut just enough to keep the hobbed bolt 
	in place; it should spin freely.

*	Insert two M3 nuts in their slots on the top of the extruder body.  
	Place an washer, then spring, then another washer on each M3 x 60mm 
	screw, then thread the screws through the slots of the idler and into
	the nuts you inserted in the extruder body.  Tighten the screws until
	the springs are well compressed (this keeps tension on the printer 
	filament).  If either spring is too short (or the bolts are too long)
	to compress properly, remove the bolt and place an M3 nut on first
	(before the washer/springs).

*	Insert the hot end into the 16mm hold on the bottom of the extruder.  

*	Secure the hot end to the extruder body by threading in two M3 x 30mm 
	screws through the front of the extruder (they will pinch the sides of 
	the hot end on their way through the plastic body).  Secure with M3
	nuts and tighten well (it is critical that the hot end be rigid and 
	not wobbly).

8.2	Connecting extruder to X-axis

*	You will need:

	a.	Extruder assembly
	b.	Wade Small Gear
	c.	One NEMA 17 motor
	d.	The plastic fan duct.
	e.	One 40mm x 40mm x 10mm fan.
	f.	Four  M4 x 25 mm screws
	g.	Four  M4 nuts
	h.	One   M3 x 30mm screw
	i.	Seven M3 x 14mm screws
	j.	Three M3 washers
	k.	One   M3 x 8mm screw
	l.	Five  M3 nuts
	m.	One   M3 locknut

*	Insert two M4 nuts in the bottom of the extruder body in the slots 
	provided.  Use pliers to gently press the nuts into the plastic, or 
	press them in with the tip of a hot soldering iron if the holes are 
	too tight.  
*	Insert two M4 nuts into the slots on the sides of the extruder body.
*	The extruder is held to the X carriage by the four M4 x 25mm screws.  
	Insert the four screws through the back of the X carriage and then 
	slide on the extruder assembly (thread the top two screws into the 
	nuts you just inserted).  Then screw the two lower M4 nuts into 
	place and tighten all four screws.
*	Insert an M3 nut into the slot on the small gear.  Use pliers or a hot
	iron to press into place if necessary.  
*	Slide the small gear onto the shaft of the NEMA 17 motor.  If 
	necessary, drill out the shaft hole on the small gear with a 5mm drill 
	bit.
*	Insert the M3 x 8mm screw and tighten against the shaft of the motor.
*	Place the motor assembly against the Wade Extruder Body (supply wires 
	upwards). Insert three M3x14 mm screws and three Ø3 mm washers without 
	tightening.  Slide the motor assembly against the Wade Big Gear and 
	tighten the screws to hold the motor secure.
*	Attach the 40mm fan to the fan duct using four M3 x 14mm screws and 
	M3 nuts.  Make sure the fan is oriented so that airflow is going toward
	the duct (usually this means the side of the fan with a label on it
	will be against the fan duct).
*	Fix the Fan Duct assembly on the Wade Extruder Body with an M3 30mm 
	screw and an M3 lock nut.  Do not overtighten.

8.3	Install glass bed

*	Now is a good time to install the glass bed.  Place the glass on top
	of the heat bed and secure with four paper-binder clips.  If the X axis
	is too low, you may have to manually turn the two Z axis rods to lift
	it high enough so that the glass will fit underneat the hot end nozzle.

9.	Connect the Electronics

*	You will need:

	a.	The electronics controller of your choice (e.g. RAMPS)
	b.	The power supply
	c.	SMART display (optional)

*	Use the checklist below as you connect the electronics.  If your 
	electronics board has multiple options for connecting devices, make a
	note of which connection you use so that you can input the settings
	to your firmware.

	[ ]	X axis stepper motor
	[ ] Y axis stepper motor
	[ ] Z axis stepper motors (2)
	[ ] Extruder stepper motor
	[ ] X axis limit switch
	[ ] Y axis limit switch
	[ ] Z axis limit switch
	[ ] Heat bed power
	[ ]	Extruder heater power
	[ ]	Extruder fan power

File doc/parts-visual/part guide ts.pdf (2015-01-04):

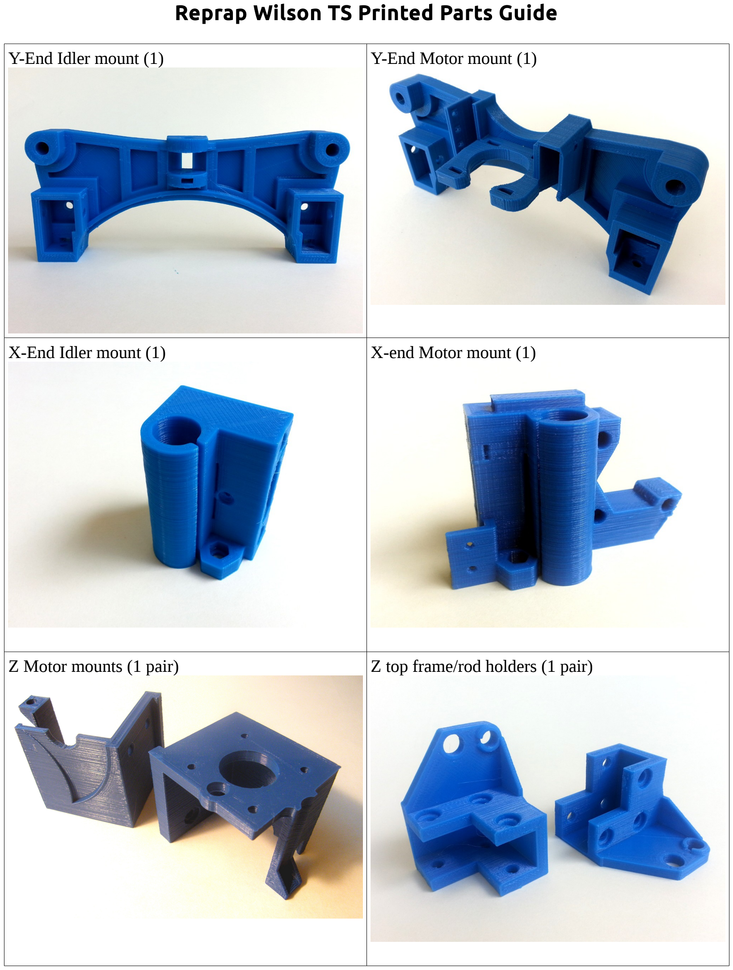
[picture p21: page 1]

Reprap Wilson TS Printed Parts Guide

Y-End Idler mount (1) | Y-End Motor mount (1)
X-End Idler mount (1) | X-end Motor mount (1)
Z Motor mounts (1 pair) | Z top frame/rod holders (1 pair)

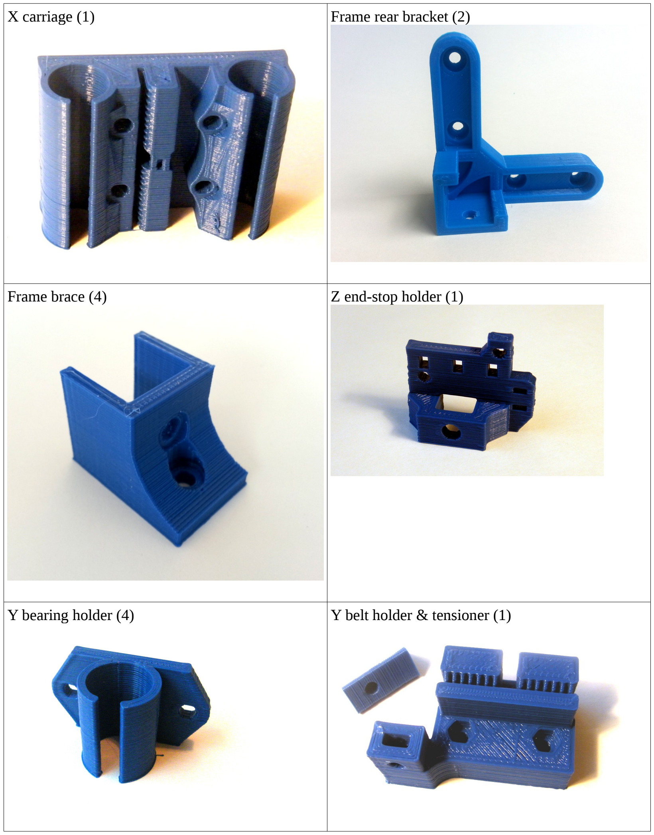
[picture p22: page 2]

X carriage (1) | Frame rear bracket (2)
Frame brace (4) | Z end-stop holder (1)
Y bearing holder (4) | Y belt holder & tensioner (1)

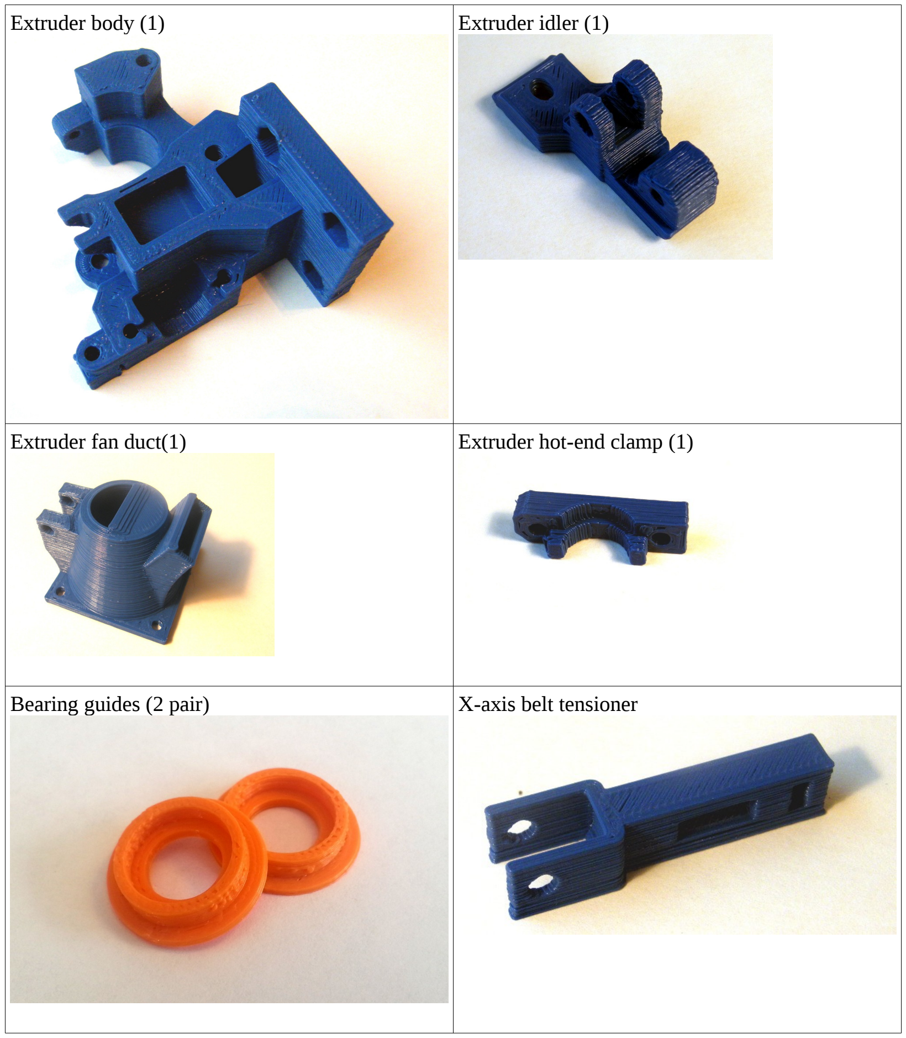
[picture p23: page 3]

Extruder body (1) | Extruder idler (1)
Extruder fan duct(1) | Extruder hot-end clamp (1)
Bearing guides (2 pair) | X-axis belt tensioner

Optional printed components

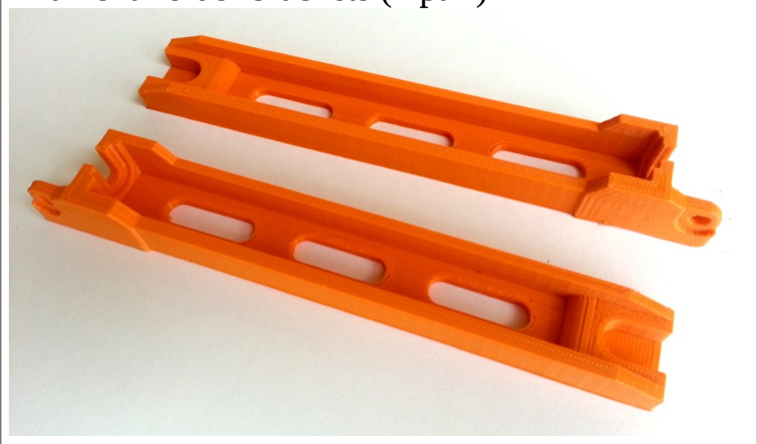
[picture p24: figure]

Ramps / Fan mount (1) | Filament holder brackets (1 pair)

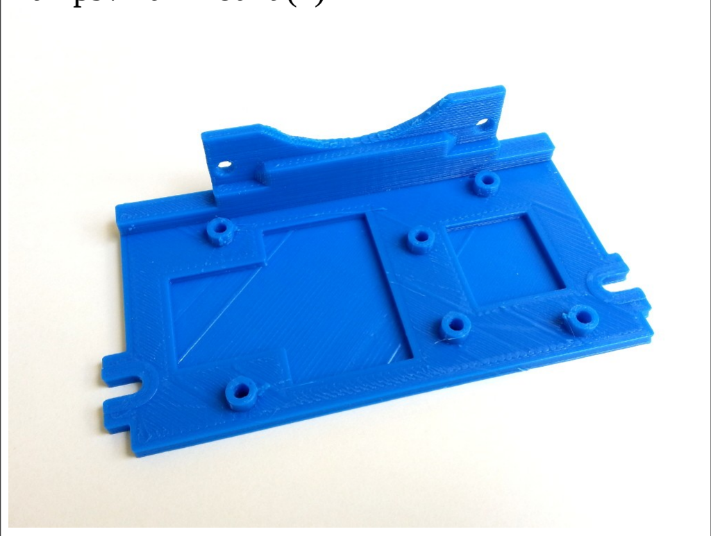
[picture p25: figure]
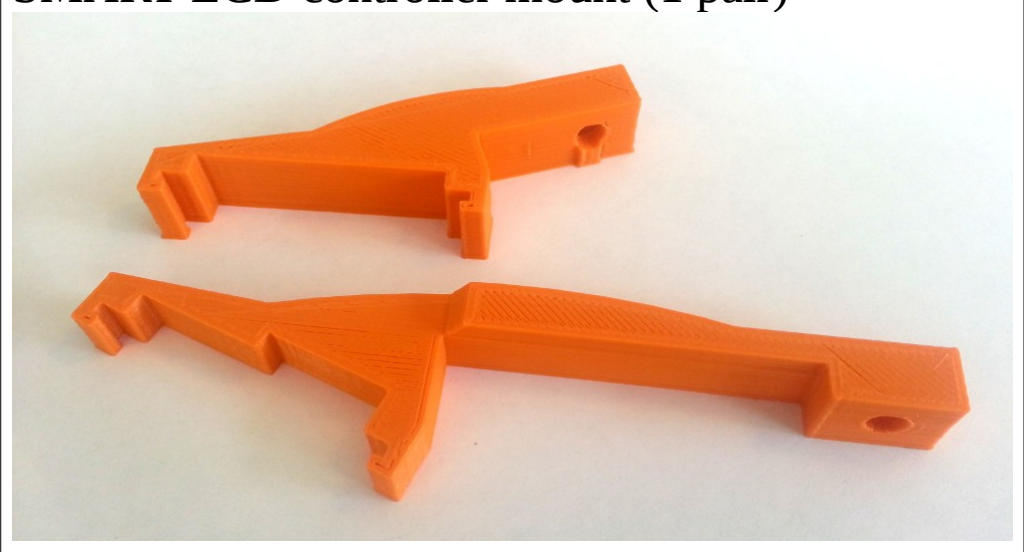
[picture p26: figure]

SMART LCD controller mount (1 pair)

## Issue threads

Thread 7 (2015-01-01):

TS model ods/wiki vs txt BOM out of sync

dantman, 2015-01-01:
I see a number of differences between the txt BOM [in git](https://github.com/mjrice/wilson/blob/master/doc/wilson-bom-ts.txt) and the .ods BOM and [wiki BOM](http://reprap.org/wiki/Wilson_TS_Bill_of_Materials) for the TS model.

Namely in the size of the horizontal and vertical 2020s and M8 x and y rods.

mjrice, 2015-01-01:
Ack, they got a little out of sync.  I've fixed them, let me know if you run into any other trouble or confusion.

dantman, 2015-01-01:
Ok, I can give you notes on the little, not immediately understandable, bits I run into as I inch toward trying to build a Wilson TS.

((I'm hoping to build myself my first 3D printer, after several months of saving up and getting parts, and decided to try making a Wilson TS instead of going with a Prusa i3 kit))

Want me to use this issue for the small bits or open new ones for them?

----

For example, my next little note would probably be this one.

When I was going over the stl files, trying to collect the list of parts I'd need printed by a third party, so I could estimate the costs, I was confused by `stl/belt-guide-sleeve-624.stl`. It isn't mentioned in the readme, wiki, or videos so I didn't know what it was for. I was confused for a little while trying to make sure that wasn't a part missting from the list. Then the commit message gave me the hint that it's an alt version of `belt-guide-624.stl` where on side snaps around the other.

dantman, 2015-01-01:
`stl/ts/extruder/` has three different extruder bodies: `extruder-body.stl`, `extruder-body-clampmountstyle.stl`, and `extruder-body-clampmountstyle-1.75mm.stl` for the original style extruder.

There's no documentation on the differences so it's not immediately obvious what one would pick / what situation determines which to use.

It's also not clear if `duct-xlong.stl` is the other version of the duct, for when using the E3D head, mentioned in [the video](http://youtu.be/z2bXSRLNdbQ).

mjrice, 2015-01-01:
I think I'll create a subfolder for stls that are still here but not usually needed, and then I'll move those other versions of things there so that the default parts are more easy to identify.  Thanks for the feedback!

mjrice, 2015-01-02:
Ok, I've done that.  I'll close this issue and if you see anything else just let me know / open a new issue.

iMattmax, 2015-03-25:
What kind of endstops are in the Wilson TS used?

Closed 2015-01-02.

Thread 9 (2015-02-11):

[Idea] E3D-v6 direct drive bowden channel

dantman, 2015-02-11:
E3D-v6 hot ends are supposed to have room to let bowden tubing go all the way down to the heat brake even when using a direct drive.

One modification idea I have is to open up the bottom of the direct drive extruder so bowden tubing can be pushed inside. This channel would go all the way up, but the plastic that guides the filament would still be there both to guide the filament and hold the bowden tubing in place.

Then a piece of bowden tubing could be cut to fit the entire E3D-v6 hot end and the extruder and fitted in when assembling.

In theory this would allow the extruder to push flexible filament directly into the tube and all the way down into hot end giving flexible filaments minimal resistance all the way to the nozzle.

I'm planning on using an E3D-v6 hot end when I build my Wilson TS in a couple of months. If no-one wants to experiment with this then, I'll probably try it.

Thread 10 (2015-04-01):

M8 replacement for M5 Rods

greenaar, 2015-04-01:
Could you release a modification to the TS model that allows for M8 rods instead of M5?  I'm about to start building one of your printers, and I'd rather do M8 for my Z axis threaded vs the M5 you have spec'd.

mjrice, 2015-04-01:
Sorry, I don't have models that would use 8mm threaded rods, and it would probably not be a simple change due to the increased size of the nuts being too close to the linear bearings for the X ends (I'm guessing).  Also, it seems like that would be a step in the wrong direction as far as accuracy and print quality.  I have been thinking of how to integrate 8mm lead screws, which is a different thing also, but it would require even more extensive changes to the design to accommodate the (even larger) copper nut used with those.

greenaar, 2015-04-01:
Understood.  It looks like I could potentially replace ..well, most of the x axis assembly with one from another model that does M8 threaded (though i may just go get some m5 rod -- is it not more wobbly for being so much thinner?)

Closed 2019-12-01.

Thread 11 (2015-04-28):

Issues when using the push fit x carriage with 3rd party printed pieces and cheap LM8UU bearings

dantman, 2015-04-28:
I had a Chinese seller print my printed parts and ordered a bunch of LM8UU bearings with extras (so I can skip the duds / rough ones). Fairly normal for starting out as I understand.

For the x carriage I picked out 3 of the best bearings in the bunch, the ones with the least resistance and popped them into the carriage.

However when I put the bearings in the carriage movement of the rod that goes in the side with 2 bearings becomes very high resistance, janky, and noisy when moving the bar hand. This is not related to any other part of the x axis or a result of one of the bearings being rough. As the bearings move relatively smoothly when not in the carriage and simply inserting a bar into the 2 bearings the resistance can be felt as you move the one bar.

I'm using the pushfit x carriage. I don't have the latest modifications, so I'm using [the earlier model](https://github.com/mjrice/wilson/blob/9de6f246761071baf5548e393ddd6ff01997b14e/stl/x-carriage-pushfit.stl).

For now I'm using a single bearing in both slots on the carriage but it may be worthwhile to resurrect a variation of the zip tie carriage model at least as a recommendation when sourcing 3rd party printed parts to build a printer from scratch. From what I recall holding bearings in place with a single zip tie (rather than two) helps the bearings self-align. Perhaps a hybrid with a push fit channel for the single bearing and 2 slots that use a single zip tie instead of two.

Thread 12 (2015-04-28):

z-motor smooth rods hole tight and has limited room for expansion

dantman, 2015-04-28:
When I had my parts printed I found the holes for the z axis smooth rods in both the [z-motors](https://github.com/mjrice/wilson/blob/master/stl/z-motors.stl) and [z-top-rodholders](https://github.com/mjrice/wilson/blob/master/stl/z-top-rodholders.stl).

Using a drill to clear out room for the rods is fine. But there is so little space around the hole in the z-motors holder I worry that attempting to actually free up as much room as was available in the assembly video would break the barrier between the smooth rod hole and motor hole.

dantman, 2015-05-14:
To workaround/solve this personally. Instead of trying to significantly widen the lower holes. I just barely widened them up enough for the rod ends to fit in. Then I widened the upper holes enough that the rods freely drop through it.

Now instead of putting the X-axis on the printer the way demonstrated in the video.

- I drop the rods through the top holes and line them up.
- I raise one rod up and lower it through the bearings on one of the of the x-axis ends with the whole axis slightly rotated away from the printer. Then I push the rod into the lower hole on the motor mount.
- I raise the other rod up and rotate the x-axis so the other end is under the rod and make sure it's lined up with the rod. Then I do the same as the first end, lower the rod into the bearings and into the lower hole.

I actually like this method of assembly compared to trying to push the whole thing up into the holes.

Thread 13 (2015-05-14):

Endstop spaces in printed parts do not have room for non-soldered limit switches using disconnect connectors

dantman, 2015-05-14:
I have a RepRapElectro RAMBo which comes with switches and connectors to use for endstops.

Instead of the limit switches having short terminal ends and being soldered to, these switches are slightly longer and a "disconnect" type connector/plug is used to attach the wires to the limit switch. This makes them a bit longer and bulkier than other endstops.
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

However none of the endstop slots on the Wilson TS have room for these switches. None are deep enough for the plugs. And some of them are shallow enough that the switches themselves don't fit properly.

Here are some photos of the switches next to the endstop slots.
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

I'll probably find some workaround to get my printer working. However it may be worthwhile to modify the printed part designs to be deep enough to accommodate these kinds of switches. The connectors do seem like a nicer idea than using solder everywhere. And they are being sold along with a board made for RepRap printers.

The Z-axis should theoretically be the easiest fix. It can simply be extended upwards a bit so there's room.

The Y-axis could be a bit trickier. A simple option would probably be to cut out a hole behind the endstop slot, that would allow the wires to simply exit from there. However it wouldn't look that nice and I'm not sure what affect if would have on the printability.

The X-axis will be the most problematic. With the threaded rod in the way there's basically no room for the endstop slot to go any deeper. And if you move it to the other side of the screw holes the switch doesn't hit the carriage.

dantman, 2015-06-05:
The x-axis is actually even worse than I thought. I bought a set of smaller switches. The z and y axis are fine with those. But the x-axis actually doesn't even fit a smaller switch ([these](http://www.robotdigg.com/product/141/Endstop,-Snap-Action-Limit-Switch-SS-5GL)).

The switch holder on the x-axis should be extended a little. But I'm starting to think that the x-axis should be redesigned so that the endstop switch is located on the back of the motor end and the back of the carriage has an extra bit of plastic that will hit it. (Though I personally have some other redesign ideas I want to try on the x-axis anyways)

mjrice, 2015-06-05:
I'm not sure why you wouldn't just solder the wires to the endstop, and then it would fit as-is.  Do you need disconnect capability on the switch?

dantman, 2015-06-05:
Technically no. But personally I like how elegant it is to simply plug in instead of messing with a soldering iron and I loath the idea of butchering the endstop cable that came with my RAMBo. Practically speaking, since there are switches sold like this in a product made for 3d printers I think it would be reasonable to support them.

Also keep in mind it's a little more involved than you think. Remember that the endstop slots on most of the axis are actually so shallow that the switches themselves sans-connector don't even fit in the slot. I'd have to take a nice switch+connector set, cut off the connectors, cut off 2/3 of the metal from the terminals on the switch, and then solder wires directly onto the switch directly onto metal (since the holes would no longer be present).

mjrice, 2015-06-06:
I'm not sure how long the terminals on your endstops are, but mine fit fine.  The switches I use are about 14mm from the lever to the end of the wiring posts, and the X axis pocket allows for 15mm.  I don't disagree with you that it's better to be compatible with as many switches as possible, but I don't fancy having to use longer rods or extrusions just to accomplish it. Mounting to the back of the X motor end isn't a bad idea either, but it would require some careful mods to the X carriage to ensure it worked consistently.  But I'd love to see what you come up with, improvements are always welcome!

dantman, 2015-06-06:
The most important measurement for the switches is probably the distance between the centre of the screw holes to the tip of the wiring posts.

The switches that came with [the RAMBo](https://reprapelectro.com/product/rambo/) measure:
- End of lever to end of wiring posts: 25mm
- Hole centre to wiring post tip: 11mm
- Wiring post length: 8.5mm
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

The ones I bought from RobotDigg measure:
- End of lever to end of wiring posts: 19.5mm
- Hole centre to wiring post tip: 6mm
- Wiring post length: 4mm
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

These fit into the y and z axis fine. But have a problem with the x-axis.

The problem there with the RobotDigg switches appears to be that the printed parts have 4-5mm between the screw holes and a wall. There is a gap with additional space but the terminals on these are 4mm perpendicular to the switch (which itself is 6mm and the terminals are in the centre). This means that the terminals do not fit into the opening.

This is my current workaround to that:
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

----

I wanted to do some modifications to the X carriage anyways. Some things I hoped to experiment with were:
- Seeing if I could apply the technique [this belt holder](https://www.youmagine.com/designs/i3-adjustable-y-belt-holder-for-gt2-t2-5) and [this clamp](https://www.youmagine.com/designs/gt2-belt-clamps) use for attaching the GT2 belts. (No vertical shifting of the belt and as a bonus, no zip ties)
- Separating the lower linear bearing holder slot into 2 holders and eliminating the plastic support in between. To see if that provides enough flex to compensate for variances in cheap linear bearings (I'm currently using one bearing in each slot instead of 3 because putting 2 in one slot basically caused my bearings to  lock up #11).
- I *might* also experiment with some of the quick change design ideas others have had and see if I can make something that works nice on the Wilson.

I was also thinking of replacing the idler tensioner with something based on [this belt connector](https://www.thingiverse.com/thing:793499)'s tensioner design. But I might hold off on that and see how well the double idler tensioner you have now works out.

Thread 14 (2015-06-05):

New Y-Motor .stl for TS that includes Y tension-er mods isn't water tight.

jmo808, 2015-06-05:
I just ran it through the cloud NetFabb/Azure model fixer and good to go. Printed perfect after.

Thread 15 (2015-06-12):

Sorry - not an issue.  Question.   What should I consider when.....

Snarfer, 2015-06-12:
Thinking about building this out with a 300mm square bed, bowden extruder, maybe 400mm high?  Would like to hear your thoughts on potential difficulties we might encounter on stretching this out.   Using Marlin firmware.  A Bowden recommendation would be appreciated.    I have always appreciated your thoughtful innovations to the Prusa - my son and I built an i3 about 3 years ago.    What head are you using?   We are considering an E3D over our original JHead.

Nice work, btw - hope your kits sell well!   I might consider buying one if I could select some mods ;)

Cheers!

mjrice, 2015-06-12:
I think that if you stretch the X axis that much, you may have more deflection in the X axis rods than you'd like.  The Y axis doesn't experience that much since the bearings are much farther apart (and it doesn't have the weight of the extuder cantilevered out like the X axis does).

As for the Z axis to 400mm, I think you'll be ok as long as you use the angled side braces and mount the machine to a wooden deck.  That will make the upright frame stiff enough that the extra height shouldn't be a problem.

I am using both the original JHeads and the e3d-lite6.  I like them both.  Hope that helps!

Snarfer, 2015-06-13:
Great point on the x-axis.   How about a 3rd rail on the x-axis?   I
thought first to just make the two thicker - but the momentum around the
current rods would make sourcing them easier.   Tweak the carriage for the
hot end to add a third rail so you could stretch it out to 400, 500?
Haha!  Stiffen up that expansion and your off and running!

On Fri, Jun 12, 2015 at 5:52 PM, Martin Rice <notifications@github.com>
wrote:

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

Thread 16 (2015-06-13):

Z-feedrate max for the Wilson

dantman, 2015-06-13:
What is the maximum z-feedrate others have been able to handle on the Wilson?
((3rd number in `#define DEFAULT_MAX_FEEDRATE {...}` in Marlin))

My threaded rods gave horrible screeches when my z-axis travelled down when I first put it together (self sourced parts) and I had to limit myself to 1 mm/s until the super lube I ordered arrived. With lubrication there's still a little metal-to-metal noise but some of it is gone.

My z stepper drivers are set to 1/4 microstepping and 1000 steps per unit. My z-feedrate max is currently set to 2 mm/s now. Setting it to 3-6 mm/s leads to my stepper motors locking.

mjrice, 2015-06-13:
Personally, I am running 2-3 mm/sec on different machines.  I have the microstepping set to 16, so 4000 steps per mm.

dantman, 2015-06-13:
IIRC with my stepper motors if I used 1/16 microstepping with 4000 steps I always ended up with my stepper motors locking up.
I wonder if there's a big difference between our stepper motors.
These are the ones I bought:
http://www.aliexpress.com/item/Free-Shipping-5pcs-4-lead-Nema17-Stepper-Motor-48mm-78Oz-in-1-8a-Nema-17-motor/1871797056.html

Or perhaps, tuning the z-axis to go faster is a matter of finding the right acceleration that gives the stepper motors time to spin up before they get to the higher speeds.

stephenci, 2015-07-13:
I have the kit and the z axis travel down screeches too. with default feedrate set at 5 per configuration.h the motor locked up. I have since change it to 2 and it works now but it also screeches. which part of the rod did you apply lubricant?

dantman, 2015-07-13:
I went a little overboard with my PTFE-fitted super-lube. Coating the whole thing (multiple times in some spots) as it was spinning and even using the gap in between the plastic that holds the nut and the rod as a kind of reservoir for lubricant, letting it coat the bar as it moved upwards.

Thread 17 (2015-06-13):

[Idea] MK8 drive gear compatible direct drive

dantman, 2015-06-13:
I've [heard good things](http://airtripper.com/1676/3d-printer-extruder-filament-drive-gear-review-benchmark/) about the the MK8 drive gear.

Perhaps it's worthwhile to make an alternate Wilson direct drive body for the MK8.

The MK8 has a smaller diameter than the MK7 so making a compatible drive would probably involve moving the stepper motor mount a little bit closer to the path the filament takes so that that path stays straight when the smaller diameter MK8 is used.

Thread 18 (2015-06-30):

cable management

stephenci, 2015-06-30:
when I looked at lulzbot mini with the cable link carrier it just look so cool I wonder if anyone has attempted to incorporate the link carrier into wilson ts? any suggestion?

dantman, 2015-07-10:
Got a picture/link of what it looks like on the LulzBot Mini? I couldn't figure out what you're referring to.

There are a lot of different types of cable management pieces on thingiverse/youmagine. Most notable would be the ones designed to attach to 2020 extrusion.

stephenci, 2015-07-13:
here you go. picture 6/8 shows a good picture of the link carriage I was referring to.

http://www.pcmag.com/slideshow_viewer/0,3253,l=331798&a=331798&po=6,00.asp

dantman, 2015-07-13:
Oh a cable chain. There are a bunch of designs for those on Thingiverse. And pull-request #6 has a design for a Wilson mount for one.

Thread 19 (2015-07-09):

No LM10UU Compatible Y-Table Model

unknownlamer, 2015-07-09:
Greetings,

I was preparing to build a Wilson with a 300mm y-axis and wanted to use 10mm rods for added stiffness (might be paranoia), and also use the Y Table instead of four bearing holders. I didn't see a parametric model for this -- could you publish a variation for fitting LM10UU bearings?

unknownlamer, 2015-07-16:
Hey,

After watching the video on the 400mm y-axis, it occurs to me now that the table probably doesn't scale very far so I've just gone ahead and printed the individual lm10uu bearing holders and tensioner.

stephenci, 2015-09-04:
are you changing the x rods to 10mm as well?

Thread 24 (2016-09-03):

No SD Card

Gordon44, 2016-09-03:
Why do I get this message No SD Card, I have a good SD card in the slot so how do I fix this problem
the unit was working just fine and now I can't see the SD Card

timmit99, 2016-09-04:
Check your lcd cables. One of them is.dedicated to the SD card operations and if it becomes loose it won't register the card as inserted. Make sure they are pressed in firmly to the adaptor and the screen.

Sent from my Verizon 4G LTE smartphone

-------- Original message --------
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

Gordon44, 2016-09-04:
Thank you that did it

----- Original Message -----
From: "timmit99" <notifications@github.com>
To: "mjrice/wilson" <wilson@noreply.github.com>
Cc: "Gordon44" <gordon1@q.com>, "Author" <author@noreply.github.com>
Sent: Saturday, September 3, 2016 7:24:43 PM
Subject: Re: [mjrice/wilson] No SD Card (#24)

Check your lcd cables. One of them is.dedicated to the SD card operations and if it becomes loose it won't register the card as inserted. Make sure they are pressed in firmly to the adaptor and the screen.

Sent from my Verizon 4G LTE smartphone

-------- Original message --------
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

Gordon44, 2016-10-25:
Hi Marty could you help me one more time

I have been using my Wilson II 3D Printer now for several months now with no problems until now

When I start the print job after I do the Bed leveling and Auto Home the printer starts to print but the print head is about 2 Inches from the bed

I tried to print using some of my older files with the same results

The print head is in the same location and has not moved

The Z offset set is set to 11.5 this is where I have been setting now for months

The Auto Home and the Bed leveling works just fine and all the switches test OK

Then when I start the job the printer starts just fine however the print head is about 2 inches above the bed

What should I do to fix this?

Thank you

Gordon Groves

Gordon1@q.com

----- Original Message -----
From: "Gordon Groves" <gordon1@q.com>
To: "mjrice/wilson" <reply@reply.github.com>
Sent: Saturday, September 3, 2016 7:48:09 PM
Subject: Re: [mjrice/wilson] No SD Card (#24)

Thank you that did it

----- Original Message -----
From: "timmit99" < notifications@github.com >
To: "mjrice/wilson" < wilson@noreply.github.com >
Cc: "Gordon44" < gordon1@q.com >, "Author" < author@noreply.github.com >
Sent: Saturday, September 3 , 2016 7:24:43 PM
Subject: Re: [mjrice/wilson] No SD Card (#24)

Check your lcd cables. One of them is.dedicated to the SD card operations and if it becomes loose it won't register the card as inserted. Make sure they are pressed in firmly to the adaptor and the screen.

Sent from my Verizon 4G LTE smartphone

-------- Original message --------
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

rodelvalle, 2016-10-25:
I know this is going to sound strange but there is a possibility it is the motor drivers.  At least for me it was. After completing both the homing and auto-level the nozzle was printing on mid-air.  If it is the same issue, you can even move the nozzle manually close to the bed.  I used for my Wilson the recommended KL17H248-15-4A.  I found that when they are in parallel (z-axis) is to much for the A4988 Stepper Motor Drive, then freezing at that precise moment.  The solution was to install instead a DRV8825 and setting the current to almost 2.7A (1.35A for each motor).  I hope this helps...

mjrice, 2016-10-25:
Hi Gordon,
When it is moving to home, does the LCD screen say "hit" next to the "Z"?
Does the endstop actually touch the bed when it is supposed to?

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

Gordon44, 2016-10-26:
When I run the program it will go to home and the print head will go down and touch the bed and beep and them say Z HIT .

After that the Z axes will move up to Z = 20 and that is where the printer will start to print from in mid air .

I have tried running other files that worked just fine it the past .

So what is going on , why will the Z axis move up to 20 and then start printing ?

Is the software bad if so should I try to reinstall it , if so can you give me the web address to down load the newest version ,
or is there something else going on that I should try .

----- Original Message -----
From : "Gordon Groves " <gordon1@q.co m>
To : "mjrice/wilson" <reply@reply.github.com>
Sent: Tuesday, October 25, 2016 6:58:20 PM
Subject: Re: [mjrice/wilson] No SD Card (#24)

Yes it does say Z Axes Hit
and yes the endstop touches the bed and beeps

----- Original Message -----
From: "Martin Rice" < notifications@github.com >
To: "mjrice/wilson" < wilson@noreply.github.com >
Cc: "Gordon44" < gordon1@q.com >, "Author" < author@noreply.github.com >
Sent: Tuesday, October 25 , 2016 3:54:18 PM
Subject: Re: [mjrice/wilson] No SD Card (#24)

Hi Gordon,
When it is moving to home, does the LCD screen say "hit" next to the "Z"?
Does the endstop actually touch the bed when it is supposed to?

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

—
You are receiving this because you authored the thread.
Reply to this email directly, view it on GitHub , or mute the thread .

Gordon44, 2016-10-26:
Yes it does say Z Axes Hit
and yes the endstop touches the bed and beeps

----- Original Message -----
From : "Martin Rice " <notifications@github.co m>
To: "mjrice/wilson" <wilson@noreply.github.com>
Cc: "Gordon44" <gordon1@q.com>, "Author" <author@noreply.github.com>
Sent: Tuesday, October 25, 2016 3:54:18 PM
Subject: Re: [mjrice/wilson] No SD Card (#24)

Hi Gordon,
When it is moving to home, does the LCD screen say "hit" next to the "Z"?
Does the endstop actually touch the bed when it is supposed to?

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

—
You are receiving this because you authored the thread.
Reply to this email directly, view it on GitHub , or mute the thread .

Gordon44, 2016-10-27:
Good news I dissemble everything and re-assembled including the Arduino and now the printer works must have been a bad connection not sure just what?

Could you email me the link to the Marlin program this website is a little confusing to just which program I should use I am planning on having a spare Arduino Mega 2560 just in case mine might go bad in the future?

Oh also do you have any plans to build a Dual Extrude head version in the near future?

Thanks for your help

Gordon

Gordon1@q.com

505 281-4495 ----- Original Message -----
From: "Gordon Groves" <gordon1@q.com>
To: "mjrice/wilson" <reply@reply.github.com>
Sent: Tuesday, October 25, 2016 7:20:59 PM
Subject: Re: [mjrice/wilson] No SD Card (#24)

When I run the program it will go to home and the print head will go down and touch the bed and beep and them say Z HIT.

After that the Z axes will move up to Z=20 and that is where the printer will start to print from in mid air.

I have tried running other files that worked just fine it the past.

So what is going on, why will the Z axis move up to 20 and then start printing?

Is the software bad if so should I try to reinstall it, if so can you give me the web address to down load the newest version,
or is there something else going on that I should try.

----- Original Message -----
From: "Gordon Groves" < gordon1@q.com >
To: "mjrice/wilson" < reply@reply.github.com >
Sent: Tuesday, October 25 , 2016 6:58:20 PM
Subject: Re: [mjrice/wilson] No SD Card (#24)

Yes it does say Z Axes Hit
and yes the endstop touches the bed and beeps

----- Original Message -----
From: "Martin Rice" < notifications@github.com >
To: "mjrice/wilson" < wilson@noreply.github.com >
Cc: "Gordon44" < gordon1@q.com >, "Author" < author@noreply.github.com >
Sent: Tuesday, October 25 , 2016 3:54:18 PM
Subject: Re: [mjrice/wilson] No SD Card (#24)

Hi Gordon,
When it is moving to home, does the LCD screen say "hit" next to the "Z"?
Does the endstop actually touch the bed when it is supposed to?

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

—
You are receiving this because you authored the thread.
Reply to this email directly, view it on GitHub , or mute the thread .

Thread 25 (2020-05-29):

Strain relief?

Xalcker, 2020-05-29:
I cannot find where is this piece needed in the assembly. Can anyone help? Is there a comunity or forma for this printer?

timmit99, 2020-05-29:
there was a forum but it seems to have lapsed and not been renewed. If I am looking at the part correctly the strain relief part is zip tied around the extruder motor and you can zip tie the extruder/toolhead wires to it. Ignore my crude MSPaint skills but this is how i envision it being used.
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

haroldj, 2020-05-29:
That piece is not really needed. I built the wilson rs about 4 years ago and it is still my go to machine and it still works great. The only thing different on mine is that I replaced the original extruder with a MK8 extruder. I have 2 other working printers, but this is still the one that gives me the best prints consistently.

timmit99, 2020-05-29:
I actually just tore apart my Wilson II after nearly 5 years of service. With my Voron 2 and Voron 0 i just didn't need the Wilson II anymore and i was having many issues with bed leveling. I'm keeping some parts as mementos though.

haroldj, 2020-05-29:
I have a wilson 2 that I built but never used because I couldn't get the config files any more after I finished the build. I have the original design with the rack and pinion levelling switch. Would you possibly have a copy of the config files? I am not good at editing arduino config files.
    On Thursday, May 28, 2020, 09:03:19 PM CDT, Tim Abraham <notifications@github.com> wrote:

I actually just tore apart my Wilson II after nearly 5 years of service. With my Voron 2 and Voron 0 i just didn't need the Wilson II anymore and i was having many issues with bed leveling. I'm keeping some parts as mementos though.

—
You are receiving this because you commented.

Reply to this email directly, view it on GitHub, or unsubscribe.

timmit99, 2020-05-29:
@haroldj i can LOOK but i switched to klipper about a year ago.

timmit99, 2020-05-29:
@haroldj wow, that was actually fast. Found my files from 11/7/16. FOR REFERENCE ONLY.  at this point i had a IR bed probe instead of the rack and pinion as i built mine before that was released.

[Configuration.txt](https://github.com/mjrice/wilson/files/4702865/Configuration.txt)
[Configuration_adv.txt](https://github.com/mjrice/wilson/files/4702866/Configuration_adv.txt)

haroldj, 2020-05-29:
Thanks a lot, that will help me a lot to get that up and running.. I was thinking of adding a regular z stop and use it that way.
    On Friday, May 29, 2020, 10:58:23 AM CDT, Tim Abraham <notifications@github.com> wrote:

@haroldj wow, that was actually fast. Found my files from 11/7/16. FOR REFERENCE ONLY. at this point i had a IR bed probe instead of the rack and pinion as i built mine before that was released.

Configuration.txt
Configuration_adv.txt

—
You are receiving this because you were mentioned.

Reply to this email directly, view it on GitHub, or unsubscribe.

Xalcker, 2020-05-29:
> there was a forum but it seems to have lapsed and not been renewed. If I am looking at the part correctly the strain relief part is zip tied around the extruder motor and you can zip tie the extruder/toolhead wires to it. Ignore my crude MSPaint skills but this is how i envision it being used.
> 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

Ok, thankyou very much. I have built a Wilson 1, and still working fine, printing some replacement parts right now.

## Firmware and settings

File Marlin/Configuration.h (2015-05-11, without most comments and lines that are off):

#define CONFIGURATION_H
#include "boards.h"
#define STRING_VERSION "1.0.3 dev"
#define STRING_VERSION_CONFIG_H __DATE__ " " __TIME__ // build date and time
#define STRING_CONFIG_H_AUTHOR "(none, default config)" // Who made the changes.
#define STRING_SPLASH_LINE1 "v" STRING_VERSION // will be shown during bootup in line 1
#define SERIAL_PORT 0
#define BAUDRATE 115200
  #define MOTHERBOARD BOARD_RAMPS_13_EFB
#define CUSTOM_MACHINE_NAME "Wilson"
#define EXTRUDERS 1
#define POWER_SUPPLY 1
#define TEMP_SENSOR_0 5
#define TEMP_SENSOR_1 0
#define TEMP_SENSOR_2 0
#define TEMP_SENSOR_3 0
#define TEMP_SENSOR_BED 60
#define MAX_REDUNDANT_TEMP_SENSOR_DIFF 10
#define TEMP_RESIDENCY_TIME 10  // (seconds)
#define TEMP_HYSTERESIS 3       // (degC) range of +/- temperatures considered "close" to the target one
#define TEMP_WINDOW     1       // (degC) Window around target to start the residency timer x degC early.
#define HEATER_0_MINTEMP 5
#define HEATER_1_MINTEMP 5
#define HEATER_2_MINTEMP 5
#define HEATER_3_MINTEMP 5
#define BED_MINTEMP 5
#define HEATER_0_MAXTEMP 275
#define HEATER_1_MAXTEMP 275
#define HEATER_2_MAXTEMP 275
#define HEATER_3_MAXTEMP 275
#define BED_MAXTEMP 150
#define PIDTEMP
#define BANG_MAX 255 // limits current to nozzle while in bang-bang mode; 255=full current
#define PID_MAX BANG_MAX // limits current to nozzle while PID is active (see PID_FUNCTIONAL_RANGE below); 255=full current
  #define PID_FUNCTIONAL_RANGE 10 // If the temperature difference between the target temperature and the actual temperature
  #define PID_INTEGRAL_DRIVE_MAX PID_MAX  //limit for the integral term
  #define K1 0.95 //smoothing factor within the PID
    #define  DEFAULT_Kp 22.2
    #define  DEFAULT_Ki 1.08
    #define  DEFAULT_Kd 114
#define PIDTEMPBED
#define MAX_BED_POWER 255 // limits duty cycle to bed; 255=full current
    #define  DEFAULT_bedKp 441.29
    #define  DEFAULT_bedKi 54.3
    #define  DEFAULT_bedKd 896.54
#define PREVENT_DANGEROUS_EXTRUDE
#define PREVENT_LENGTHY_EXTRUDE
#define EXTRUDE_MINTEMP 170
#define EXTRUDE_MAXLENGTH (X_MAX_LENGTH+Y_MAX_LENGTH) //prevent extrusion of very large distances.
#define THERMAL_RUNAWAY_PROTECTION_PERIOD 40 //in seconds
#define THERMAL_RUNAWAY_PROTECTION_HYSTERESIS 4 // in degree Celsius
#define THERMAL_RUNAWAY_PROTECTION_BED_PERIOD 20 //in seconds
#define THERMAL_RUNAWAY_PROTECTION_BED_HYSTERESIS 2 // in degree Celsius
#define ENDSTOPPULLUPS // Comment this out (using // at the start of the line) to disable the endstop pullup resistors
const bool X_MIN_ENDSTOP_INVERTING = false; // set to true to invert the logic of the endstop.
const bool Y_MIN_ENDSTOP_INVERTING = false; // set to true to invert the logic of the endstop.
const bool Z_MIN_ENDSTOP_INVERTING = false; // set to true to invert the logic of the endstop.
const bool X_MAX_ENDSTOP_INVERTING = false; // set to true to invert the logic of the endstop.
const bool Y_MAX_ENDSTOP_INVERTING = true; // set to true to invert the logic of the endstop.
const bool Z_MAX_ENDSTOP_INVERTING = true; // set to true to invert the logic of the endstop.
const bool Z_PROBE_ENDSTOP_INVERTING = false; // set to true to invert the logic of the endstop.
#define DISABLE_MAX_ENDSTOPS
#define X_ENABLE_ON 0
#define Y_ENABLE_ON 0
#define Z_ENABLE_ON 0
#define E_ENABLE_ON 0 // For all extruders
#define DISABLE_X false
#define DISABLE_Y false
#define DISABLE_Z false
#define DISABLE_E false // For all extruders
#define DISABLE_INACTIVE_EXTRUDER true //disable only inactive extruders and keep active extruder enabled
#define INVERT_X_DIR false
#define INVERT_Y_DIR false
#define INVERT_Z_DIR false
#define INVERT_E0_DIR true
#define INVERT_E1_DIR false
#define INVERT_E2_DIR false
#define INVERT_E3_DIR false
#define X_HOME_DIR -1
#define Y_HOME_DIR -1
#define Z_HOME_DIR -1
#define min_software_endstops true // If true, axis won't move to coordinates less than HOME_POS.
#define max_software_endstops true  // If true, axis won't move to coordinates greater than the defined lengths below.
#define X_MIN_POS 0
#define Y_MIN_POS 0
#define Z_MIN_POS 0
#define X_MAX_POS 200
#define Y_MAX_POS 200
#define Z_MAX_POS 200
#define Z_PROBE_REPEATABILITY_TEST  // If not commented out, Z-Probe Repeatability test will be included if Auto Bed Leveling is Enabled.
#define HOMING_FEEDRATE {200, 200, 200, 0}  // set the homing speeds (mm/min)
#define DEFAULT_AXIS_STEPS_PER_UNIT   {80,80,4000,100}  // default steps per unit for Ultimaker
#define DEFAULT_MAX_FEEDRATE          {200, 200, 5, 25}    // (mm/sec)
#define DEFAULT_MAX_ACCELERATION      {3000,3000,100,10000}    // X, Y, Z, E maximum start speed for accelerated moves. E default values are good for Skeinforge 40+, for older versions raise them a lot.
#define DEFAULT_ACCELERATION          3000    // X, Y, Z and E acceleration in mm/s^2 for printing moves
#define DEFAULT_RETRACT_ACCELERATION  3000   // E acceleration in mm/s^2 for retracts
#define DEFAULT_TRAVEL_ACCELERATION   3000    // X, Y, Z acceleration in mm/s^2 for travel (non printing) moves
#define DEFAULT_XYJERK                10.0    // (mm/sec)
#define DEFAULT_ZJERK                 0.4     // (mm/sec)
#define DEFAULT_EJERK                 5.0    // (mm/sec)
#define CUSTOM_M_CODES
#define EEPROM_SETTINGS
  #define EEPROM_CHITCHAT // please keep turned on if you can.
#define PLA_PREHEAT_HOTEND_TEMP 180
#define PLA_PREHEAT_HPB_TEMP 50
#define PLA_PREHEAT_FAN_SPEED 0   // Insert Value between 0 and 255
#define ABS_PREHEAT_HOTEND_TEMP 220
#define ABS_PREHEAT_HPB_TEMP 100
#define ABS_PREHEAT_FAN_SPEED 0   // Insert Value between 0 and 255
#define LANGUAGE_INCLUDE GENERATE_LANGUAGE_INCLUDE(en)
  #define DISPLAY_CHARSET_HD44780_JAPAN        // this is the most common hardware
#define REPRAP_DISCOUNT_SMART_CONTROLLER
#define SOFT_PWM_SCALE 0
#define FILAMENT_SENSOR_EXTRUDER_NUM 0   //The number of the extruder that has the filament sensor (0,1,2)
#define MEASUREMENT_DELAY_CM        14   //measurement delay in cm.  This is the distance from filament sensor to middle of barrel
#define DEFAULT_NOMINAL_FILAMENT_DIA 1.75 //Enter the diameter (in mm) of the filament generally used (3.0 mm or 1.75 mm) - this is then used in the slicer software.  Used for sensor reading validation
#define MEASURED_UPPER_LIMIT         2 //upper limit factor used for sensor reading validation in mm
#define MEASURED_LOWER_LIMIT         1.5 //lower limit factor for sensor reading validation in mm
#define MAX_MEASUREMENT_DELAY       20   //delay buffer size in bytes (1 byte = 1cm)- limits maximum measurement delay allowable (must be larger than MEASUREMENT_DELAY_CM  and lower number saves RAM)
#define DEFAULT_MEASURED_FILAMENT_DIA  DEFAULT_NOMINAL_FILAMENT_DIA  //set measured to nominal initially
#include "Configuration_adv.h"
#include "thermistortables.h"

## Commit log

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2014-02-01 trying to move files bah
    [y-end-idler.stl, y-end-motor.stl]
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2014-02-01 added z rod holders
    [z-top-rodholders.stl]
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2014-02-01 beam bracket and xends
    [frame-beam-bracket.stl, x-end-idler.stl, x-end-motor.stl]
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2014-02-04 added filament holder supports
    [filamentholder.stl]
2014-02-04 added holder for SMART lcd controller
    [smartmount.stl]
2014-02-09 X end idler update
    [x-end-idler.stl]
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2014-02-09 added openscad source folder
    [bearing.scad, tensioner.scad, x-end-idler.scad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]
2014-02-13 updated x-end motor with adjuster block
    [x-end-motor.scad, x-end-motor.stl]
2014-02-14 added y ends and belt holder
    [bearing.scad, configuration.scad, frame-beam-bracket.stl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]
2014-02-14 fixed beam bracket stl
    [frame-beam-bracket.stl]
2014-02-17 bom updated with belt lengths
    [wilson-bom.ods]
2014-02-20 added electronics checklist and more to bom
    [wilson-bom.ods]
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2014-02-22 new RP part images, updated 624 guide
    [belt-guide-624.scad, belt-guide-624.stl, wilson-bom.ods]
2014-02-26 upgraded Y braces for strength, M5x10mm for same
    [WADE-BIG-GEAR.stl, frame-beam-bracket.stl, frame-rearbrackets.stl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]
2014-02-26 update ramps holder, y end idler scad fix
    [ramps-mount.stl, y-end-idler.scad]
2014-02-26 z rod inserts widened .15mm, were too tight
    [z-motors.stl, z-top-rodholders.stl]
2014-02-26 ramps mount moved 4mm away from x motor
    [ramps-mount.stl]
2014-02-27 fixed dimension error on previous version
    [z-top-rodholders.stl]
2014-03-02 adding TS y ends
    [y-idler-ts.stl, y-motor-ts.stl]
2014-03-02 moving rs y ends to stl/rs
    [y-end-idler.stl, y-end-motor.stl]
2014-03-02 update z mounts, better z axis range
    [frame-beam-bracket.stl, z-motors.stl, z-top-rodholders.stl]
2014-03-02 minor adj to y ends
    [y-idler-ts.stl, y-motor-ts.stl]
2014-03-02 adding sgraber frame brace, update bearing holder
    [frame-brace-v2.stl, y-bearing-holder.stl]
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2014-03-02 some new images, added ts frame brace scad
    [frame-brace-v2.scad, frame-brace-v2.stl]
2014-03-03 added svelt rear bracket option for TS
    [frame-rear-bracket-ts.stl]
2014-03-03 minor adj to yend slots
    [y-idler-ts.stl, y-motor-ts.stl]
2014-03-03 better 624 belt guide version
    [belt-guide-sleeve-624.stl]
2014-03-04 ts support in bom spreedsheet, few other additions
    [belt-guide-624-uni.scad, filamentholder.stl, wilson-bom.ods]
2014-03-04 minor adj to y end idler slot and slight enlargement of y motor screw slots
    [y-idler-ts.stl, y-motor-ts.stl]
2014-03-05 added y belt holder for TS
    [y-belt-holder-ts.scad, y-belt-holder-ts.stl]
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2014-03-14 slight material reduction on zmotors, improved endstop mount on xmotor
    [x-end-motor.stl, z-motors.stl]
2014-03-18 update TS models, minor changes for fit
    [frame-brace-v2.stl, frame-rear-bracket-ts.stl, y-idler-ts.stl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]
2014-03-18 update bom with updated rod lengths
    [wilson-bom.ods]
2014-03-26 added missing rp parts to bom
    [wilson-bom.ods]
2014-03-27 replaced original rear bracket with the TS version (recommended for all)
    [frame-rear-brackets.stl, frame-rearbrackets.stl]
2014-04-06 new extruder body and herringbone gears
    [biggear.stl, extruder-body.stl, smallgear.stl]
2014-04-06 removed old extruder body and gears
    [BODY-EXTRUDEUR-WADE-with-support.stl, WADE-BIG-GEAR.stl, WADE-SMALL-GEAR.stl]
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2014-04-12 put back rear frame bracket for RS, the TS version interfers with RS beam bracket
    [frame-rear-bracket-rs.stl]
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2014-04-29 added MCAD for gears; updated bom with fixes; removed old X carriage; added ATX holder brackets
    [2Dshapes.scad, X-CARRIAGE.stl, alphabet_block.scad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]
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2014-06-21 update Y ends, Y belt holder with new tensioner, and extruder parts for better printing/fit
    [FAN-DUCT.stl, biggear.stl, extruder-body.stl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]
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2014-06-22 some additions to bom, some other sync updates minor stuff
    [extruder.skp, gears.scad, wilson-bom.ods]
2014-07-07 added tensioners for x and y, a few other refinements
    [wilson-bom.ods, x-carriage.stl, x-tensioner.stl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]
2014-07-08 better printability on bearing holder and x carrage
    [x-carriage.stl, y-bearing-holder.stl]
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2014-08-03 numerous tiny fit adjustments, and added my marlin configuration file for reference
    [Configuration.h, bearing.scad, biggear.stl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]
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2014-09-07 added new pushfit x-carriage model (no zip ties, prints vertically)
    [x-carriage-pushfit.stl]
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2014-10-03 added pushfit beaing holders for y axis, in both original LM8UU size and LM10UU for the plus size she-printers. Eliminates 8 zip ties from the build.
    [y-bearing-holder-lm10uu.stl, y-bearing-holder-lm8uu-nozip.stl]
2014-10-08 updated extruder sketchup models and some minor tweaks
    [extruder.skp, x-end-idler.stl, x-end-motor.stl]
2014-10-08 added models for Y ends that use 10mm smooth rods instead of the default 8mm
    [y-idler-ts-10mm-rods.stl, y-motor-ts-10mm-rods.stl]
2014-10-11 removed old ramps mount, fixed new ramps mount mesh
    [belt-guide-624.stl, ramps-mount-redux.stl, ramps-mount.stl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]
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2015-01-01 sync'd up spreedsheet and TS build bom (txt) and added extruder option to ods
    [wilson-bom.ods]
2015-01-02 Reorganized and moved lesser common parts into stl/alts
    [FAN-DUCT-E3D.stl, FAN-DUCT-ORIG.stl, FAN-DUCT-widemouth.stl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]
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2015-01-04 tweaked direct drive extruder
    increased the support for filament by extending the tube a little closer
    to the drive gear, to help with bendy filaments that want to buckle.
    [extruder-direct-drive.stl]
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2015-01-25 Updated extruder to 2-spring ver, added 0.5mm more thickness to frame screw holes
    [extruder-direct-drive.stl, frame-rear-brackets-ts-pair.stl, frame-rear-brackets-ts.stl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]
2015-02-04 miniscule tweak to x end rod slots, added some new assembly photos in docs
    [bearing.scad, smartmount.stl, x-end-idler.stl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]
2015-04-12 update direct drive skethcup model and xcarriage stl w/orientation emblem
    [extruder-direct-drive.skp, x-carriage-pushfit.stl]
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2015-05-19 adding y-table and y-tensioner, which replace y bearing holders and y belt holder
    [y-tensioner.stl, ytable-8mm.stl]
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
